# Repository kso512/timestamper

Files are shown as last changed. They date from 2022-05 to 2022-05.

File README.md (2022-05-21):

# timestamper

*timestamper:* A Time Stamp Printer

## Introduction

The goal of this project is quickly and easily generating a series of unique slips of paper, for use in labeling and other forms of keeping things in order.

## User Stories

The primary "user story" is: the user comes home from the grocery store with lots of items, and would like to affix unique timestamps on each while putting them away.  After counting the number of items, the device can be powered on and set to generate that number of items. It will then print that many unique timestamp slips.  Scissors and tape can be used to separate them from each other, and adhere them to the groceries, respectively.  This allows older items to be easily identified, especially if care is taken to place "younger" timestamp slips on "younger" groceries per available "created on" or "best by" dates.

Secondarily, one-offs can be created and added to more significant projects, such as mounting something to a wall, putting together furniture, or marking a special time.

Generally, if a unique yet anonymous hard-copy identifier is needed, and a rate of one-per-second is fast enough, this might work for you!

## Operation

Outputs are a LCD panel (20 columns by 4 rows) to display text, a NeoPixel to indicate status by color, and a "count.txt" file on the CircuitPython drive to retain that number between boots.  The NeoPixel will show green for configuring, blue for awaiting input, and red for taking action based on a button press or file write.

Input is received from the user via the rotary encoder and the integrated switch.  By turning the rotary encoder and watching the "Count" presented on the LCD panel, the user can tell the timestamper how many slips to print.  Once a proper count is selected, the user can then depress the integrated switch and the timestamper will retrieve the current time and begin printing.

## Hardware Setup

### Required Hardware

* [Adafruit QT Py ESP32-S2 WiFi Dev Board with uFL Antenna Port - STEMMA QT](https://www.adafruit.com/product/5348)
  * Central processing of inputs/outputs
  * Update date/time via wifi
* [2.4GHz Mini Flexible WiFi Antenna with uFL Connector - 100mm](https://www.adafruit.com/product/2308)
  * This antenna (or something similar) is needed for the QT Py to achieve a decent wifi signal
* [20x4 LCD display](https://www.adafruit.com/product/198)
  * Used to indicate how many timestamps to print, status, etc.
* [i2c/SPI LCD Backpack](https://www.adafruit.com/product/292)
  * Connects LCD display to QT Py over SPI bus
* [Rotary Encoder in CircuitPython](https://www.adafruit.com/product/377)
  * Rotate to set number of iterations (timestamps to generate)
  * Press to execute
* [Mini Thermal Receipt Printer Starter Pack](https://www.adafruit.com/product/600)
  * Prints timestamps from QT Py over serial bus, via voltage divider
  * Starter pack includes critical components such as a power supply and connectors
* Resistors for voltage divider (5VDC -> 3.3VDC), one each
  * 2.2k
  * 3.3k

### Building

See the included Fritzing file (`timestamper.fzz`) for "breadboard" and "schematic" views, which show all the required connections.  Use a breadboard at first, then transfer and solder onto something more permanent like a Perma-Proto once everything is working.

To act as an enclosure, I used a plastic tub and lid.  The lid acts as a "panel" to mount the printer and user interface to, and the tub contains the wires and spare paper rolls.

#### Prototype Unit

From left to right: thermal printer, breadboard, LCD Panel with backpack; on the breadboard, from left to right: rotary encoder, voltage divider, QT Py with antenna

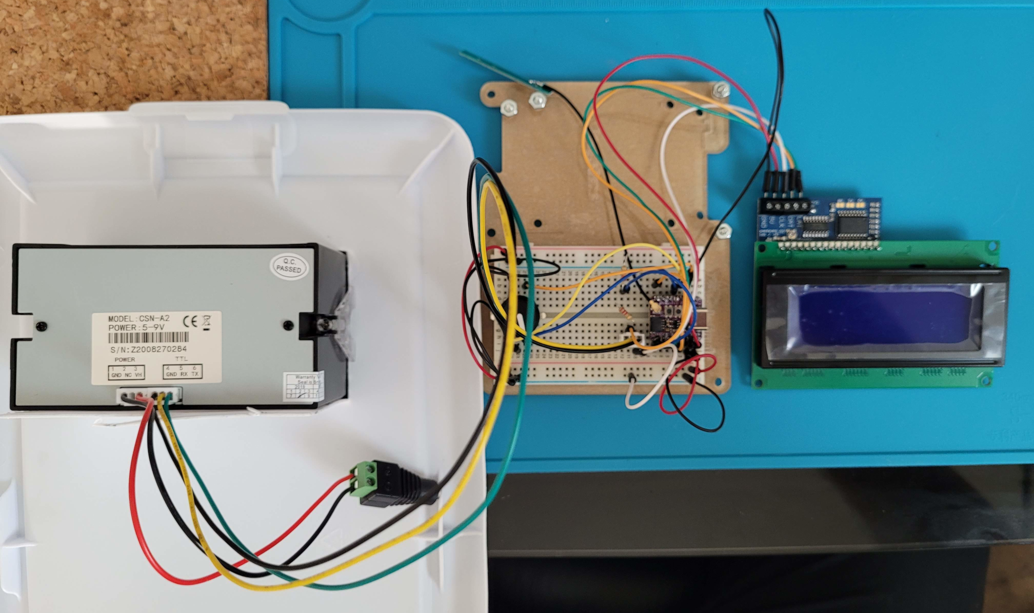
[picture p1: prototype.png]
Picture of prototype unit


#### Assembled Unit

Internal view from left to right: thermal printer, perma-proto board, LCD Panel with backpack; on the perma-proto board, from top to bottom: voltage divider, LCD panel connector, rotary encoder (on reverse side), QT Py with antenna

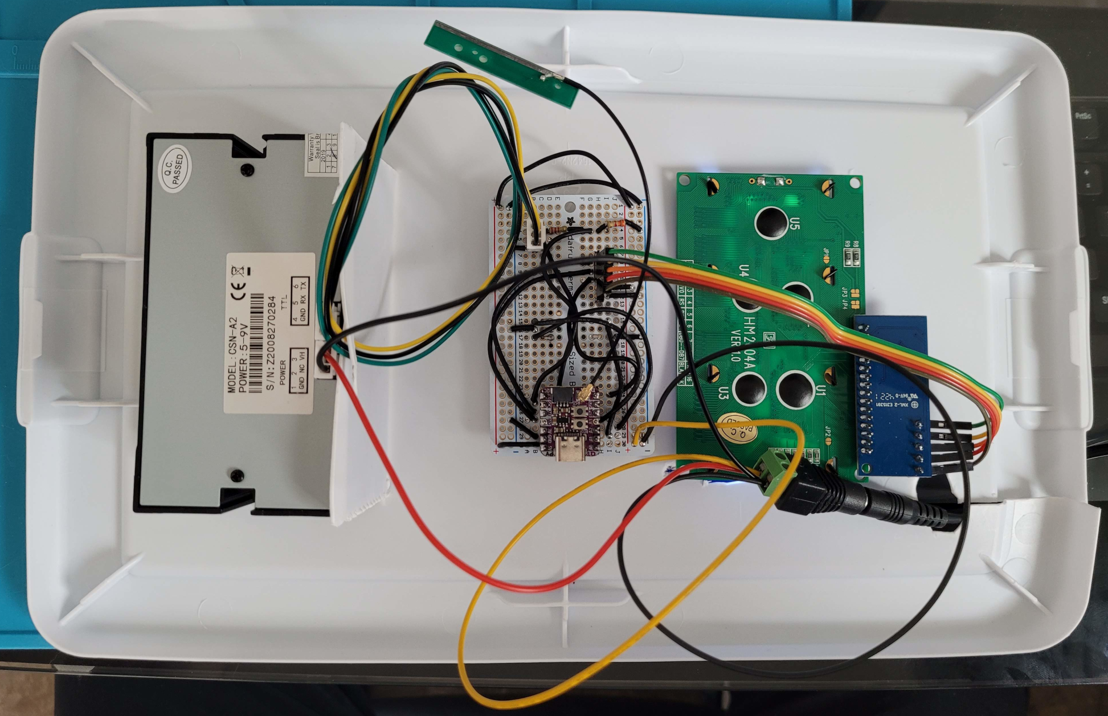
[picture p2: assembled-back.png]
Picture of assembled unit, back


External view from left to right: thermal printer, rotary encoder, LCD panel

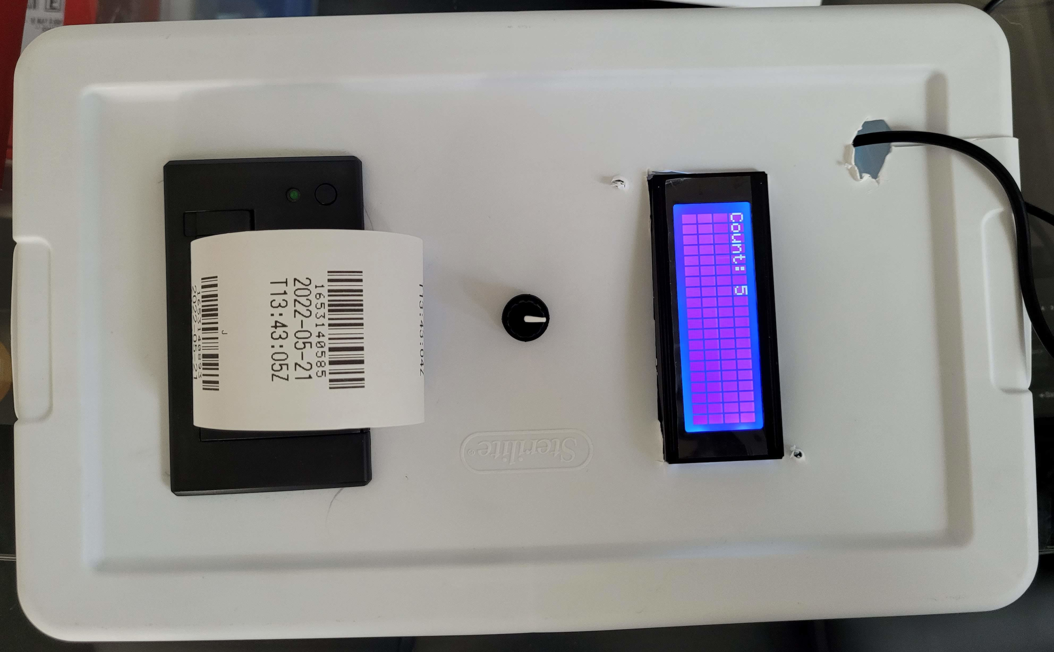
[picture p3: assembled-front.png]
Picture of assembled unit, front


### Consumables

* Thermal receipt printer paper
* Clear packing tape

**NOTE**: Test your combination of paper and tape for fading by printing some test slips and applying tape directly to the "inked" surface.  If fading occurs within a week, try another tape/paper combination, or use a small inverted (sticky-to-sticky) piece of tape to protect the "inked" surface from the adhesive that would touch it.

## Software Setup

* [Flash the QT Py with CircuitPython](https://learn.adafruit.com/adafruit-qt-py-esp32-s2/circuitpython), so a new drive named `CIRCUITPY` is created.
* Create on the `CIRCUITPY` drive:
  * A `secrets.py` file with [WiFi SSID and credentials](https://learn.adafruit.com/adafruit-qt-py-esp32-s2/circuitpython-internet-test#secrets-file-3077419-5)
* Copy to the `CIRCUITPY` drive:
  * The required libraries from the [Adafruit CircuitPython Library Bundle](https://docs.circuitpython.org/projects/bundle/en/latest/), under the `/lib` folder:
    * [adafruit_74hc595](https://docs.circuitpython.org/projects/74hc595/en/latest/)
    * [adafruit_character_lcd](https://docs.circuitpython.org/projects/character_lcd/en/latest/)
    * [adafruit_datetime](https://docs.circuitpython.org/projects/datetime/en/latest/)
    * [adafruit_requests](https://docs.circuitpython.org/projects/requests/en/latest/)
    * [adafruit_thermal_printer](https://docs.circuitpython.org/projects/thermal_printer/en/latest/)
  * `boot.py`
  * `code.py`

Example secrets.py:

    $ cat /media/user/CIRCUITPY/secrets.py
    secrets = {
        'ssid' : 'ChangeToYourWifiSSID',
        'password' : 'ChangeToYourWifiPassword',
        }

Required files and folder structure:

    $ tree /media/user/CIRCUITPY/
    /media/user/CIRCUITPY/
    ├── boot.py
    ├── code.py
    ├── lib
    │   ├── adafruit_74hc595.py
    │   ├── adafruit_character_lcd
    │   │   ├── character_lcd_i2c.py
    │   │   ├── character_lcd.py
    │   │   ├── character_lcd_rgb_i2c.py
    │   │   ├── character_lcd_spi.py
    │   │   └── __init__.py
    │   ├── adafruit_datetime.py
    │   ├── adafruit_requests.py
    │   ├── adafruit_thermal_printer
    │   │   ├── __init__.py
    │   │   ├── thermal_printer_2168.py
    │   │   ├── thermal_printer_264.py
    │   │   ├── thermal_printer_legacy.py
    │   │   └── thermal_printer.py
    │   └── neopixel.py
    └── secrets.py
    
    3 directories, 17 files

## Design Goals & Decisions

* Efficient code - only call out to the Internet as needed, not each loop
* Freshness over independence - doesn't rely on internal counters
* Long-term - works as well the 100th time as the 1st time
* Low-power - uses less power than the existing Raspberry Pi solution, aims to minimize power consumption in the future
* Portable - only needs a power cable; gets online without a network cable
* Ratcheting - avoids creating two records twice, always incrementing and avoiding overruns of previous work
* Robust - tests for failures and handles them gracefully; does not assume everything goes perfect every time
* Simple to use - one knob to turn, one button to press
* User-friendly - build a high barrier between the user and failure scenarios, such as continuing after a failure, telling the user they are wrong for trying to use zero or a negative number when allowed by the interface, etc.

## TODO / Future Improvements

### Automation

* Include QR-codes for encoding more data than a barcode
* Integrations with webhooks/APIs to update online databases/inventories

### Power conservation

* Relay, transistor, etc. to control power to the thermal printer
* Standby mode to reduce overall power consumption

### Storage

* Total timestamps generated
* Log of each timestamp generated

### User Interface

* Fine-tune code to closer meet Design Goals & Decisions
* Add screenshots and pictures
* Use the Neo-Pixel to indicate status or activity, beyond what's shown on the LCD panel
* Maybe go ahead and add a RTC, or go full-blown GPS

## Pitfalls and Lessons Learned

While initially it appeared useful, the [adafruit_ntp](https://docs.circuitpython.org/projects/ntp/en/latest/api.html) library appears to require a very specific ESP32 SPI integration that the ESP32-S2 unit available does not possess.  That is why the "long way" is used to pull a URL, then extract a useable time from that.  Copying/pasting the sample code results in this error:

    Traceback (most recent call last):
    File "code.py", line 9, in <module>
    AttributeError: 'module' object has no attribute 'ESP_CS'

Printing as fast as possible without reliable tracking of previous runs can allow for duplicate timestamps to be created, which goes against the whole idea of unique slips of paper.  Early prototype example generated by repeatedly pressing the button and the `time.sleep(1)` line commented out:

    -> Button pressed! Printing 1 timestamps...
    -> Timestamp:
    1652661770
    2022-05-16T00:42:50Z
    -> Printing complete! Awaiting rotary input to set Position; press button to print...
    -> Button pressed! Printing 1 timestamps...
    -> Timestamp:
    1652661770
    2022-05-16T00:42:50Z
    -> Printing complete! Awaiting rotary input to set Position; press button to print...

## References

* [Adafruit IO Time Service](https://io.adafruit.com/api/docs/#time)
* [Adafruit Learning System](https://learn.adafruit.com/)
  * [i2c/SPI LCD Backpack](https://learn.adafruit.com/i2c-spi-lcd-backpack)
  * [Rotary Encoder in CircuitPython](https://learn.adafruit.com/rotary-encoder)
  * [Adafruit QT Py ESP32-S2 WiFi Dev Board with uFL Antenna Port - STEMMA QT](https://learn.adafruit.com/adafruit-qt-py-esp32-s2)
  * [Mini Thermal Receipt Printer](https://learn.adafruit.com/mini-thermal-receipt-printer)
* [CircuitPython Reference Documentation](https://docs.circuitpython.org/en/latest/README.html)
  * [adafruit_74hc595](https://docs.circuitpython.org/projects/74hc595/en/latest/)
  * [adafruit_character_lcd](https://docs.circuitpython.org/projects/character_lcd/en/latest/)
  * [adafruit_datetime](https://docs.circuitpython.org/projects/datetime/en/latest/)
  * [adafruit_requests](https://docs.circuitpython.org/projects/requests/en/latest/)
  * [adafruit_thermal_printer](https://docs.circuitpython.org/projects/thermal_printer/en/latest/)
* [W3Schools](https://www.w3schools.com/)
  * [Python Functions](https://www.w3schools.com/python/python_functions.asp)
  * [Python Math](https://www.w3schools.com/python/python_math.asp)
  * [Python String join() Method](https://www.w3schools.com/python/ref_string_join.asp)
  * [Python String split() Method](https://www.w3schools.com/python/ref_string_split.asp)
  * [Python String splitlines() Method](https://www.w3schools.com/python/ref_string_splitlines.asp)
  * [Python try Keyword](https://www.w3schools.com/python/ref_keyword_try.asp)

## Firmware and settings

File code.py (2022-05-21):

# Based on demo code at: https://learn.adafruit.com

# Needed for multiple reasons:
import board
import busio
import digitalio
# Needed for internet access: and fetching URLs
import ipaddress
import wifi
import ssl
import socketpool
import adafruit_requests
# Needed for date/time/string processing:
import time
from adafruit_datetime import datetime
# Needed for rotary encoder integration:
import rotaryio
# Needed for LCD panel integration:
import adafruit_character_lcd.character_lcd_spi as character_lcd
# Needed for Thermal Printer integration:
import adafruit_thermal_printer.thermal_printer_legacy
# Needed for NeoPixel and storage integration:
import neopixel

# URL to fetch:
TEXT_URL = "https://io.adafruit.com/api/v2/time/seconds"
# Number of seconds to delay start-up as CircuitPython seems to reload
# multiple times when saving files
DELAY_SEC = 2
# Number of printer lines to use as a buffer
LINE_FEED = 2
# Set to false to save paper when testing non-printing functions
USE_PAPER = True
# IP address to ping during configuration
ipv4 = ipaddress.ip_address("8.8.4.4")
# Initialize these for later use
button_state = None
last_position = None

print("-> Powered on! Hello World! Pausing to allow for reloads...")
time.sleep(DELAY_SEC)
print("-> Pause complete! Configuring...")

# Configure NeoPixel
pixel = neopixel.NeoPixel(board.NEOPIXEL, 1)
# Green for configuring
pixel.fill((0, 255, 0))

# Configure button switch as digital with pull-up resistor
# Button switch pin = "A1" aka "GPIO17" aka "D17"
button = digitalio.DigitalInOut(board.D17)
button.direction = digitalio.Direction.INPUT
button.pull = digitalio.Pull.UP

# Configure rotary encoder inputs
# Encoder pins = "A2"/"A3" aka "GPIO8"/"GPIO9" aka "D8"/"D9"
# Arrange "D8"/"D9" as needed below to set direction
encoder = rotaryio.IncrementalEncoder(board.D9, board.D8)

# Configure LCD character panel
spi = busio.SPI(board.SCK, MOSI=board.MOSI)
latch = digitalio.DigitalInOut(board.D37)
cols = 20
rows = 4
lcd = character_lcd.Character_LCD_SPI(spi, latch, cols, rows)

# Configure thermal printer
uart = busio.UART(board.TX, board.RX, baudrate=19200)
ThermalPrinter = adafruit_thermal_printer.get_printer_class(2.16)
printer = ThermalPrinter(uart)

def say(*tuple):
    "Function to simplify output"
    print("-> " + " ".join(tuple))
    lcd.message = " ".join(tuple)
    return

say("My MAC addr:" + str([hex(i) for i in wifi.radio.mac_address]) + "\nConfiguring...")

# Get wifi details and more from a secrets.py file
try:
    from secrets import secrets
except ImportError:
    say("WiFi secrets are kept in secrets.py, please add them there!")
    raise

# Try to get online
say("Attempting connection to %s"%secrets["ssid"])
try:
    wifi.radio.connect(secrets["ssid"], secrets["password"])
    say("Connected to %s!"%secrets["ssid"])
except:
    say("Unable to connect to %s!"%secrets["ssid"])
    say("Available WiFi networks:")
    for network in wifi.radio.start_scanning_networks():
        say("\t%s\t\tRSSI: %d\tChannel: %d" % (str(network.ssid, "utf-8"),
                network.rssi, network.channel))
    wifi.radio.stop_scanning_networks()
    raise

# Show online information and set up networking
say("My IP address is", str(wifi.radio.ipv4_address))
say("Ping google.com: %f ms" % (wifi.radio.ping(ipv4)*1000))

pool = socketpool.SocketPool(wifi.radio)
requests = adafruit_requests.Session(pool, ssl.create_default_context())

def fetch_time(str):
    "This function accepts a URL and returns an integer Unix timestamp"
    say("Fetching text from:", str)
    try:
        response = requests.get(str)
    except:
        say("Unable to fetch", str)
        raise
    output = int(response.text)
    return output

# Pull the time as a test, but don't say
unixtime = fetch_time(TEXT_URL)
out_string = datetime.fromtimestamp(unixtime).isoformat() + "Z"
say("Test timestamp:", out_string)

# Try to load a saved file and use it if found
try:
    with open("/count.txt", "r") as count_log:
        position_original = int(count_log.read())
        say("Loaded saved Count: " + str(position_original))
except:
    position_original = 0
    say("No saved count to load")

say("Configured! Awaiting rotary input to adjust Count; press button to print...")
# Light blue for awaiting input
pixel.fill((0, 0, 128))

# Input-gathering loop
while True:
    position_delta = int(encoder.position)
    position = position_original + position_delta
    if last_position is None or position != last_position:
        lcd.clear()
        say("Count: %d"%position)
    last_position = position
    if not button.value and button_state is None:
        button_state = "pressed"
    if button.value and button_state == "pressed":
        # Light red for input received
        pixel.fill((128, 0, 0))
        # Assume that if the button is pressed, we want at least one timestamp
        if position == 0: position = 1
        # Assume that a negative count should be positive
        position = abs(position)
        # Log the new position/count
        try:
            with open("/count.txt", "w") as count_log:
                    # Brighten the NeoPixel on every write...
                    pixel.fill((255, 0, 0))
                    count_log.write('{}\n'.format(position))
                    count_log.flush()
                    pixel.fill((128, 0, 0))  # Then return it to light red
        except OSError as e:  # When the filesystem is NOT writable by CircuitPython...
            delay = 0.5  # ...blink the NeoPixel every half second.
            if e.args[0] == 28:  # If the file system is full...
                delay = 0.15  # ...blink the NeoPixel every 0.15 seconds!
            while True:
                pixel.fill((255, 0, 0))
                time.sleep(delay)
                pixel.fill((0, 0, 0))
                time.sleep(delay)
        lcd.clear()
        say("Button pressed! Preparing to print %d timestamps..."%position)
        # Pull the time once, then count up from there
        unixtime = fetch_time(TEXT_URL)
        # Iterate up from zero so we can track our position
        for i in range(0, position):
            # Build the time from our iteration plus our fetched time
            loop_time = unixtime + i
            # Generate our ISO-8601 time stamp
            out_datetime = datetime.fromtimestamp(loop_time).isoformat() + "Z"
            # Split the ISO-8601 time stamp into date and time
            out_split = out_datetime.split("T")
            # The date is just the first item in the list we just made
            out_date = out_split[0]
            # The time is the second item in the list, plus the T we lost above
            out_time = "T" + out_split[1]
            # Build the final string, which doesn't need loop_time because
            # it's included in the barcode output
            out_string = out_date + "\n" + out_time
            display_string = "Printing: " + str(i + 1) + " of " + str(position) + "\n" + str(loop_time) + "\n" + out_string
            lcd.clear()
            say(display_string)
            if (USE_PAPER == True):
                # Center justify
                printer.justify = adafruit_thermal_printer.JUSTIFY_CENTER
                # Print the barcode
                printer.print_barcode(str(loop_time), printer.CODE128)
                # Large size
                printer.size = adafruit_thermal_printer.SIZE_LARGE
                # Print the output
                printer.print(out_string)
                # Give a little room at the bottom
                printer.feed(LINE_FEED)
            # Wait one second so we can't overlap previous runs
            time.sleep(1)
        button_state = None
        say("Printing complete! Awaiting rotary input to adjust Count; press button to print...")
        # Light blue for awaiting input
        pixel.fill((0, 0, 128))
        # Re-draw the final screen to leave a clean display
        lcd.clear()
        say("Count: %d"%position)
